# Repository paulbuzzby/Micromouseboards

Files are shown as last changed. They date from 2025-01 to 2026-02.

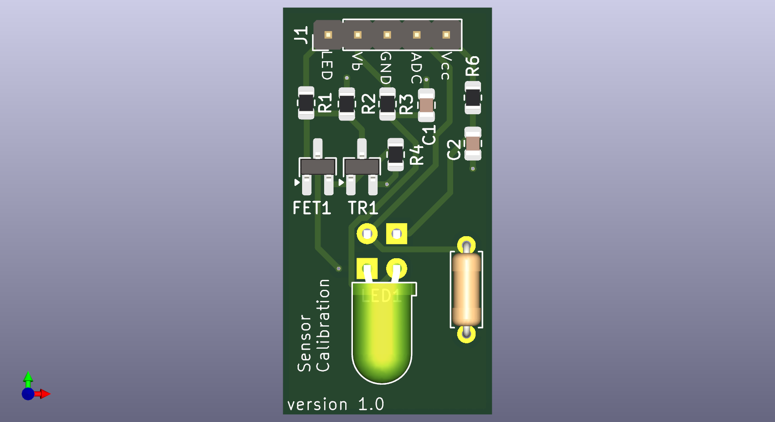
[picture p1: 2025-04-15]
SensorCalibrationBoard/SensorCalibrationBoardTop.png

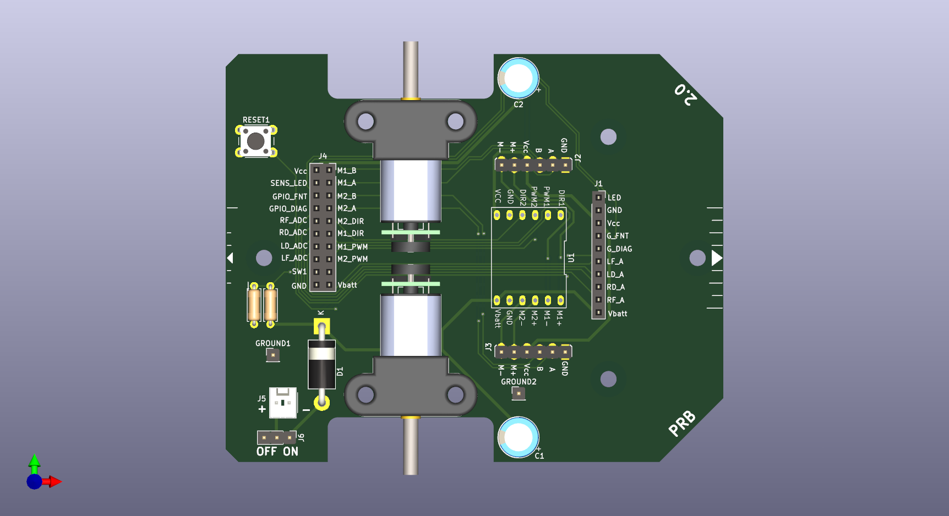
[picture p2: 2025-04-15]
SSChassisBoard/SSChassisBoardTop.png

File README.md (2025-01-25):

# Micromouseboards
Here are different sets of PCBs for various Micro Mouse applications. This is the start of me using KiCad. I make no promises that any of this works.

Some of these boards (MouseSMDUKMARSAdvancedBoard and MouseMainboardTemplate) started as UKMARS boards that can be found [Here](https://github.com/ukmars/ukmarsbot)

All credit to Peter Harrison for the original design of these boards

Circuit design for the other boards is credited to Duncan Louttit

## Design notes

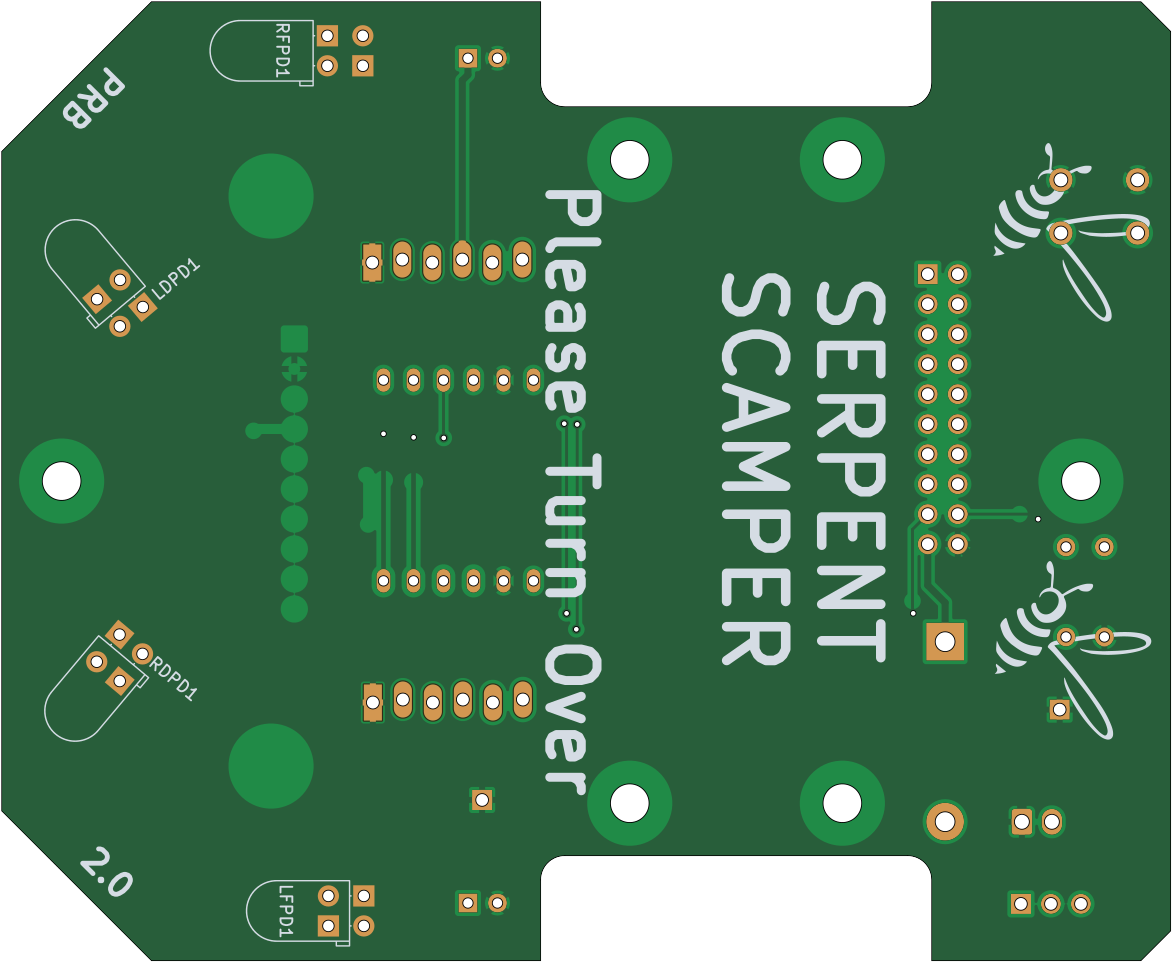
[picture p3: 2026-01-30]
docs/SSChassisAndSensorBoard/SSChassisAndSensorBoard_board_bottom.png

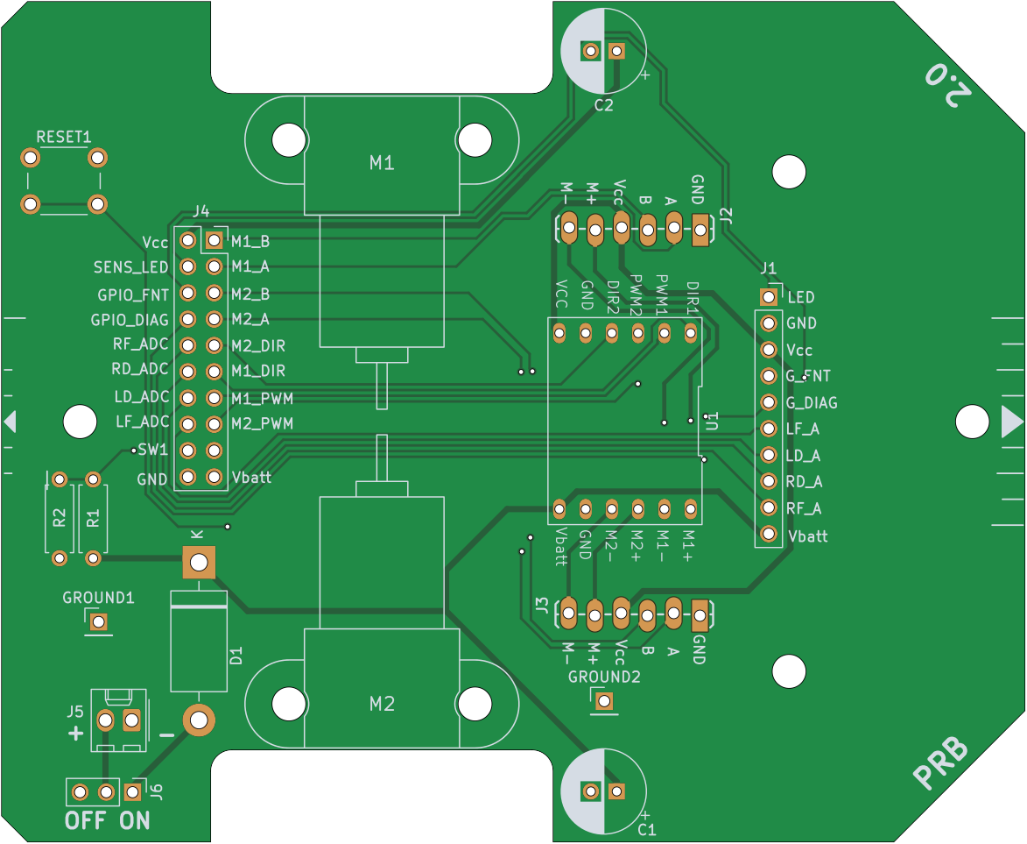
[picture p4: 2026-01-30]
docs/SSChassisBoard/SSChassisBoard_board_top.png

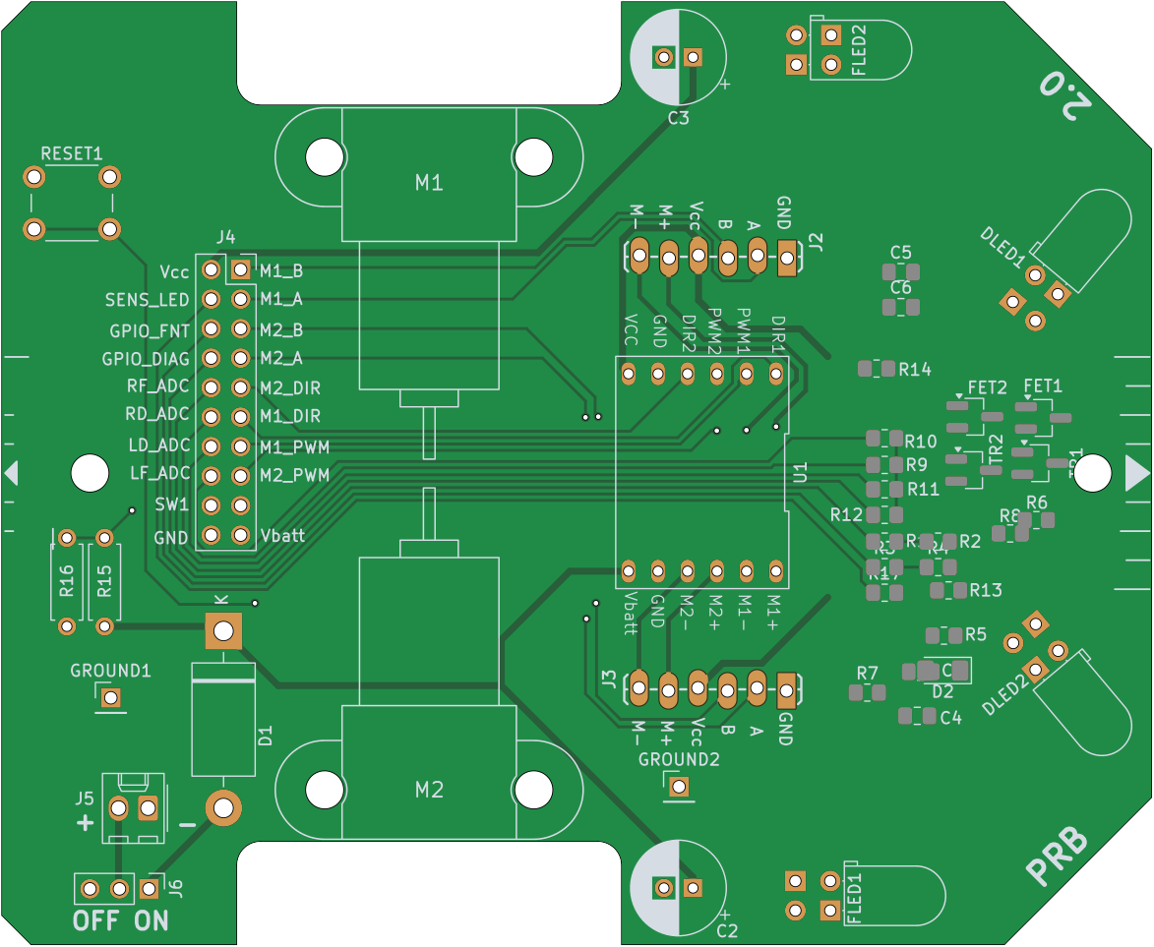
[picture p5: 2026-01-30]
docs/SSChassisAndSensorBoard/SSChassisAndSensorBoard_board_top.png

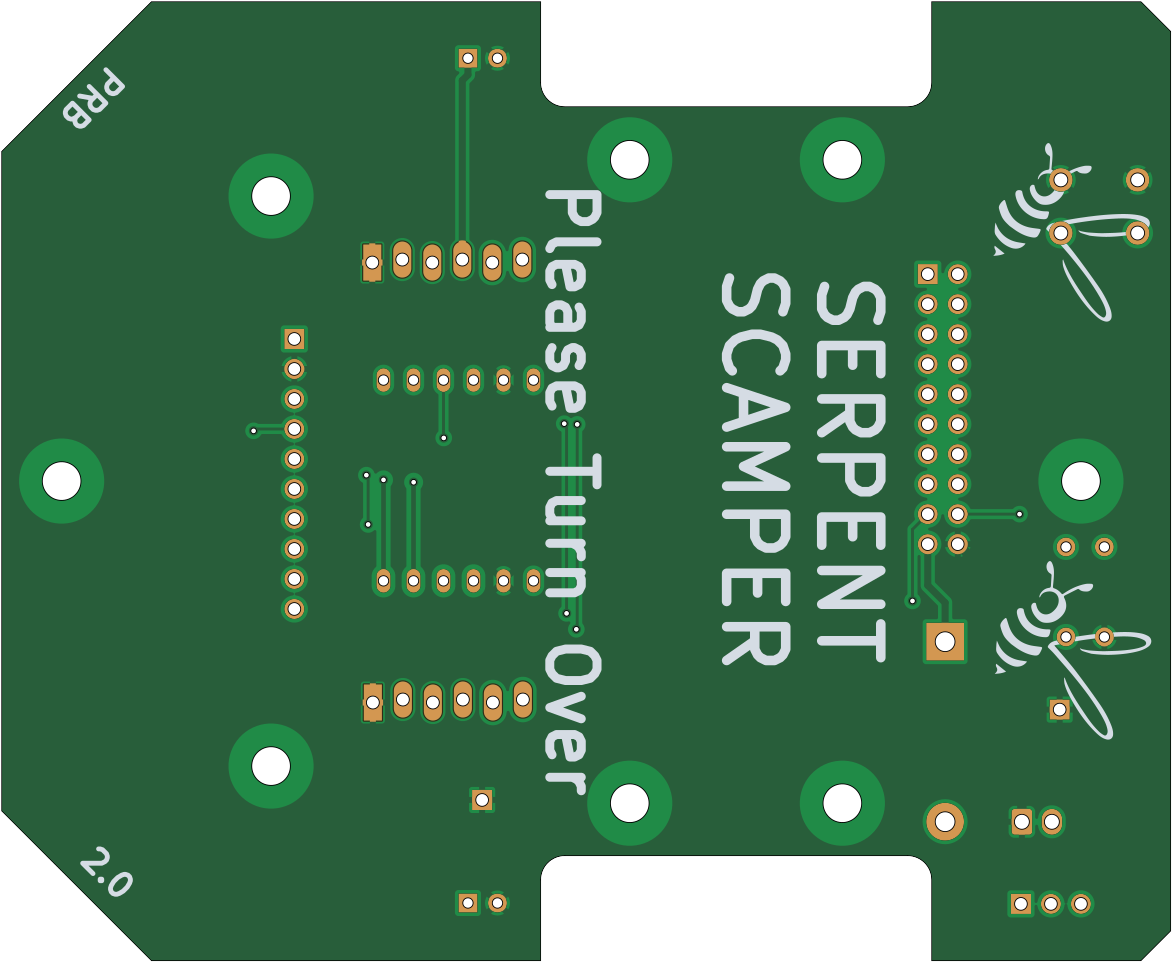
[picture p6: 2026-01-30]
docs/SSChassisBoard/SSChassisBoard_board_bottom.png

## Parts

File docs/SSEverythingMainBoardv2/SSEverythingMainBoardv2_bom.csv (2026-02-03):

Reference | Value | Qty | Note | Description
A1 | Arduino_Nano_RP2040_Connect | 1 |  | Arduino Nano board based on the RP2040 microcontroller with a dual-core 133 MHz ARM Cortex-M0+ processor, 264 kB SRAM, and up to 16 MB flash memory. Operates at 3.3V, with 5V Micro USB input and 4-20V VIN. Features Wi-Fi®, Bluetooth® LE, digital and analog pins, and supports SPI, I2C, UART, and PIO. Includes a 6-axis IMU, RGB LED, microphone, and cryptographic chip for secure communication.
C1 C2 C3 C5 C7 C8 C9 C10 | 10uF | 8 |  | Unpolarized capacitor
C4 C6 | 330uF, 16V | 2 | Maximum height is 10mm
D3 D4 D5 | LED | 3 |  | Light emitting diode
FLLED1 FRLED2 LDLED1 RDLED2 | TLCR5800 | 4 |  | Light emitting diode
GROUND1 GROUND2 J4 J5 J6 J8 | GROUND | 6 |  | Generic connector, single row, 01x01, script generated (kicad-library-utils/schlib/autogen/connector/) Generic connector, single row, 01x02, script generated (kicad-library-utils/schlib/autogen/connector/) Generic connector, single row, 01x05, script generated (kicad-library-utils/schlib/autogen/connector/) Generic connector, single row, 01x03, script generated (kicad-library-utils/schlib/autogen/connector/)
J1 J2 | CONN_06SILK_FEMALE_PTH | 2 | 6 pin header, 0.1", male
LDPD1 LFPD1 RDPD1 RFPD1 | BPW96B | 4 |  | Photodiode
M1 | Left MOTOR | 1 | commercial mounts need bushing for screws
M2 | Right MOTOR | 1 | commercial mounts need bushing for screws
Q1 Q2 Q3 Q4 | PBSS4160DS | 4
R3 R4 | 100K | 2 |  | Resistor
R5 R7 R15 R22 | 100R | 4 |  | Resistor
R1 R2 R17 R18 R19 R20 | 1K | 6 |  | Resistor
R21 | 1K0 | 1 |  | Resistor
R12 R14 R24 R25 | 220R | 4 |  | Resistor
R9 R10 R11 R13 | 2K2 | 4 |  | Resistor
R6 R8 R16 R23 | 4R7 | 4 |  | Resistor
SW1 | TACT_SW | 1 |  | TACT switch 6mm 4.5mm
U1 | DFRobot_DC_Controller | 1

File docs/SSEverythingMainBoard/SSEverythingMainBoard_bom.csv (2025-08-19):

Reference | Value | Qty | Note | Description
A1 | Arduino_Nano_RP2040_Connect | 1 |  | Arduino Nano board based on the RP2040 microcontroller with a dual-core 133 MHz ARM Cortex-M0+ processor, 264 kB SRAM, and up to 16 MB flash memory. Operates at 3.3V, with 5V Micro USB input and 4-20V VIN. Features Wi-Fi®, Bluetooth® LE, digital and analog pins, and supports SPI, I2C, UART, and PIO. Includes a 6-axis IMU, RGB LED, microphone, and cryptographic chip for secure communication.
C7 C8 C10 C12 | 0.1uF | 4
C1 C2 C3 C5 C9 C11 | 10uF | 6 |  | Unpolarized capacitor
C4 C6 | 330uF, 16V | 2 | Maximum height is 10mm
D3 D4 D5 | LED | 3 |  | Light emitting diode
D2 | SS34 | 1 | RS - 808-0433 | onsemi 40V 3A, Schottky Diode
DLED1 DLED2 FLED1 FLED2 | TLCR5800 | 4 |  | Light emitting diode
FET1 FET2 | PMV45EN2 | 2 |  | N-Channel MOSFET, 5.1 A, 30 V, 3-Pin SOT-23
GROUND1 GROUND2 J3 J4 J5 J6 | GROUND | 6 | 0.1" pitch, polarised, any type | Generic connector, single row, 01x01, script generated (kicad-library-utils/schlib/autogen/connector/) Generic connector, single row, 01x02, script generated (kicad-library-utils/schlib/autogen/connector/) Generic connector, single row, 01x05, script generated (kicad-library-utils/schlib/autogen/connector/)
J1 J2 | CONN_06SILK_FEMALE_PTH | 2 | 6 pin header, 0.1", male
LDPD1 LFPD1 RDPD1 RFPD1 | BPW96B | 4 |  | Photodiode
M1 | Left MOTOR | 1 | commercial mounts need bushing for screws
M2 | Right MOTOR | 1 | commercial mounts need bushing for screws
R3 R4 | 100K | 2 |  | Resistor
R5 R7 | 10R | 2 |  | Resistor
R19 | 180K | 1 |  | Resistor
R17 R18 | 1K | 2 |  | Resistor
R21 | 1K0 | 1 |  | Resistor
R1 R2 R12 R14 | 220R | 4 |  | Resistor
R20 | 68K | 1 |  | Resistor
R9 R10 R11 R13 | R | 4 |  | Resistor
R6 R8 | R56 | 2 |  | Resistor
SW1 | TACT_SW | 1 |  | TACT switch 6mm 4.5mm
TR1 TR2 | BC849 | 2 |  | 0.1A Ic, 30V Vce, NPN Transistor, SOT-23
U1 | DFRobot_DC_Controller | 1

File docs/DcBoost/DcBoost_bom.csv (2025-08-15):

Reference | Value | Qty | Note | Description
C2 | 10uF | 1 |  | Unpolarized capacitor
C1 | 2.2uF | 1 |  | Unpolarized capacitor
D1 | SS34 | 1 |  | Schottky diode, small symbol, filled shape
L1 | L4.7uH | 1 |  | Inductor
R2 | R10k | 1 |  | Resistor
R1 | R64.9k | 1 |  | Resistor
U1 | MIC2288 | 1 |  | DC Boost

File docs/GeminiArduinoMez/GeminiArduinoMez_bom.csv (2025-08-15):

Reference | Value | Qty | Note | Description
A1 | Arduino_Nano_RP2040_Connect | 1 |  | Arduino Nano board based on the RP2040 microcontroller with a dual-core 133 MHz ARM Cortex-M0+ processor, 264 kB SRAM, and up to 16 MB flash memory. Operates at 3.3V, with 5V Micro USB input and 4-20V VIN. Features Wi-Fi®, Bluetooth® LE, digital and analog pins, and supports SPI, I2C, UART, and PIO. Includes a 6-axis IMU, RGB LED, microphone, and cryptographic chip for secure communication.
D1 | LED | 1 |  | Light emitting diode
J1 J3 J4 | Conn_01x16 | 3 |  | Generic connector, single row, 01x16, script generated (kicad-library-utils/schlib/autogen/connector/) Generic connector, single row, 01x06, script generated (kicad-library-utils/schlib/autogen/connector/)
R2 | 180K | 1 |  | Resistor
R1 | 680R | 1 |  | Resistor
R3 | 68K | 1 |  | Resistor
SW1 | TACT_SW | 1 |  | TACT switch 6mm 4.5mm

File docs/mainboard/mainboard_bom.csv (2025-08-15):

Reference | Value | Qty | Note | Description
C2 | 330uF, 16V | 1 | Maximum height is 10mm
D1 | 1N5401 | 1 | > 2A rectifier. Shottky is good
J2 J3 | CONN_06SILK_FEMALE_PTH | 2 | 6 pin header, 0.1", male
J4 | POWER | 1 | 0.1" pitch, polarised, any type
J1 | SENSORS | 1 | 14 pin header, 0.1", male
M1 | Left Motor | 1 | commercial mounts need bushing for screws
M2 | Right Motor | 1 | commercial mounts need bushing for screws
S1 | sub-miniature, SPDT | 1 | Toggle or slide, 0.1" pitch pins, EG Salecom TS-4-TE1CR-E-H-Z03

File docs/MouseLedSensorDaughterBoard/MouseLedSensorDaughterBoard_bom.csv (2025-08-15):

Reference | Value | Qty | Note | Description
J2 | Conn_01x04 | 1 |  | Generic connector, single row, 01x04, script generated (kicad-library-utils/schlib/autogen/connector/)
LED1 | TLCR5800 | 1 |  | Light emitting diode
PD3 | BPW96B | 1 |  | Phototransistor NPN
PD2 | QSB34 | 1 |  | Photodiode VEMD4010X01

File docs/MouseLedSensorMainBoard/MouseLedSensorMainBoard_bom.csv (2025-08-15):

Reference | Value | Qty | Note | Description
C1 C2 | 10uF | 2 |  | Unpolarized capacitor
FET1 | BSH108,215 | 1 |  | 5mA Idss, 30V Vgs, N-Channel JFET, SOT-23
J1 J2 | Conn_01x05 | 2 |  | Generic connector, single row, 01x06, script generated (kicad-library-utils/schlib/autogen/connector/) Generic connector, single row, 01x08, script generated (kicad-library-utils/schlib/autogen/connector/)
R3 | 10R | 1 |  | Resistor
R1 R4 | 220R | 2 |  | Resistor
RPD1 | 100K | 1 |  | Resistor
RSENSE1 | R56 | 1 |  | Resistor
S1R1 S2R1 | R | 2 |  | Resistor
TR1 | BC849 | 1 |  | 0.1A Ic, 30V Vce, NPN Transistor, SOT-23

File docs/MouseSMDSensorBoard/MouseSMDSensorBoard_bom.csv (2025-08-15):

Reference | Value | Qty | Note | Description
C1 C2 | 10uF | 2 |  | Unpolarized capacitor
FET1 | PMV45EN2 | 1 |  | N-Channel MOSFET, 5.1 A, 30 V, 3-Pin SOT-23
J1 | Conn_01x05 | 1 |  | Generic connector, single row, 01x05, script generated (kicad-library-utils/schlib/autogen/connector/)
LED1 | TLCR5800 | 1 |  | Light emitting diode
PD2 | BPW96B | 1 |  | Photodiode
PD1 | QSB34 | 1 |  | Photodiode QSB34 (RS part number 805-0508)
R2 | 100K | 1 |  | Resistor
R3 | 10R | 1 |  | Resistor
R1 R6 | 220R | 2 |  | Resistor
R5 | R | 1 |  | Resistor
R4 | R56 | 1 |  | Resistor
TR1 | BC849 | 1 |  | 0.1A Ic, 30V Vce, NPN Transistor, SOT-23

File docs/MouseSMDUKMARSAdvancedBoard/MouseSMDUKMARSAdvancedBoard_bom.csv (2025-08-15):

Reference | Value | Qty | Note | Description
C1 C2 C3 C4 | 10uF | 4 |  | Unpolarized capacitor
D1 | LED | 1 |  | Light emitting diode
DLED1 DLED2 FLED1 FLED2 | TLCR5800 | 4 |  | Light emitting diode
FET1 FET2 | PMV45EN2 | 2 |  | N-Channel MOSFET, 5.1 A, 30 V, 3-Pin SOT-23
J1 | Conn_01x10 | 1 |  | Generic connector, single row, 01x10, script generated (kicad-library-utils/schlib/autogen/connector/)
LDPD1 LFPD1 RDPD1 RFPD2 | BPW96B | 4 |  | Photodiode
R3 R4 | 100K | 2 |  | Resistor
R5 R7 | 10R | 2 |  | Resistor
R15 | 1K0 | 1 |  | Resistor
R1 R2 R12 R14 | 220R | 4 |  | Resistor
R9 R10 R11 R13 | R | 4 |  | Resistor
R6 R8 | R56 | 2 |  | Resistor
TR1 TR2 | BC849 | 2 |  | 0.1A Ic, 30V Vce, NPN Transistor, SOT-23

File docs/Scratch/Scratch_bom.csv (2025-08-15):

Reference | Value | Qty | Note | Description
C1 C2 | 330uF, 16V | 2 | Maximum height is 10mm
D1 | 1N5401 | 1 | > 2A rectifier. Shottky is good
GROUND1 GROUND2 J1 J4 J5 J6 | GROUND | 6 | 0.1" pitch, polarised, any type | Generic connector, single row, 01x01, script generated (kicad-library-utils/schlib/autogen/connector/) Generic connector, single row, 01x10, script generated (kicad-library-utils/schlib/autogen/connector/) Generic connector, double row, 02x10, odd/even pin numbering scheme (row 1 odd numbers, row 2 even numbers), script generated (kicad-library-utils/schlib/autogen/connector/) Generic connector, single row, 01x03, script generated (kicad-library-utils/schlib/autogen/connector/)
J2 J3 | CONN_06SILK_FEMALE_PTH | 2 | 6 pin header, 0.1", male
M1 | Left MOTOR | 1 | commercial mounts need bushing for screws
M2 | Right MOTOR | 1 | commercial mounts need bushing for screws
R1 | 180K | 1 |  | Resistor
R2 | 68K | 1 |  | Resistor
RESET1 | TACT_SW | 1 |  | TACT switch 6mm 4.5mm
U1 | DFRobot_DC_Controller | 1
U2 | LMV331 | 1 |  | Single General-Purpose Low-Voltage Comparator, SOT-23-5/SC-70-5

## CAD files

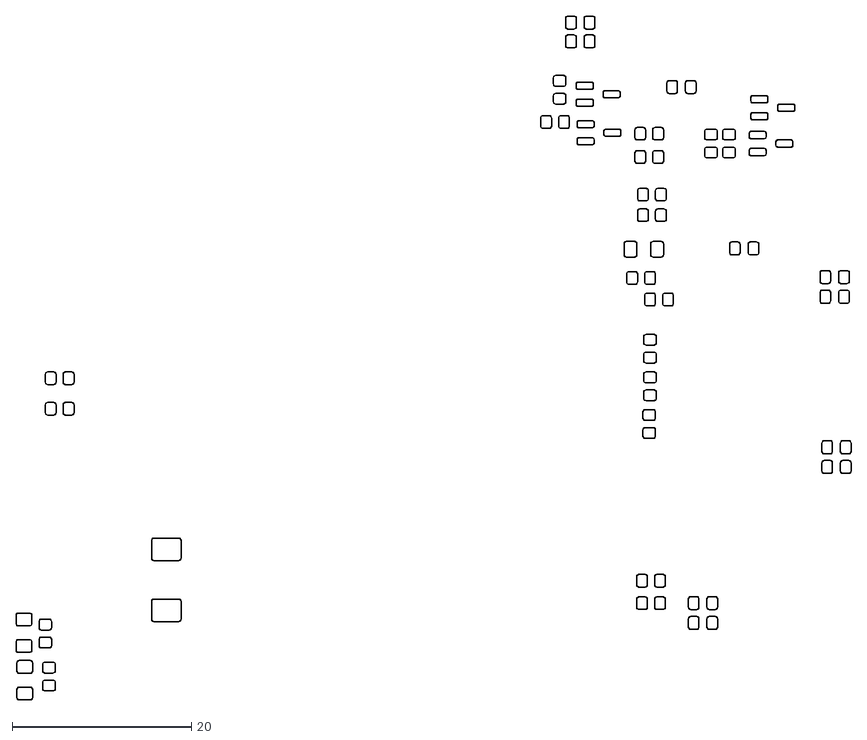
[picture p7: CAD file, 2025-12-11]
SSEverythingMainBoard/SSEverythingMainBoard-PasteTop.dxf
93.2 x 76.3

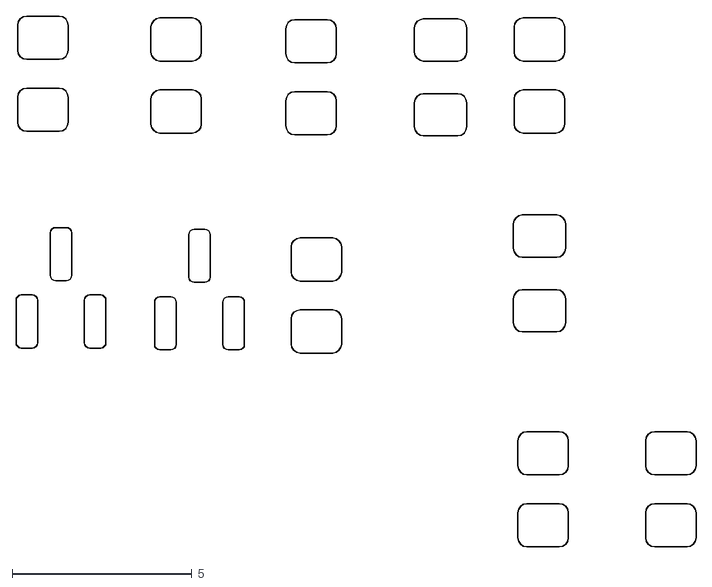
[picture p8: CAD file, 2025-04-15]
Stencils/MouseLedSensorMainBoard-PasteTop.dxf
18.9 x 14.8

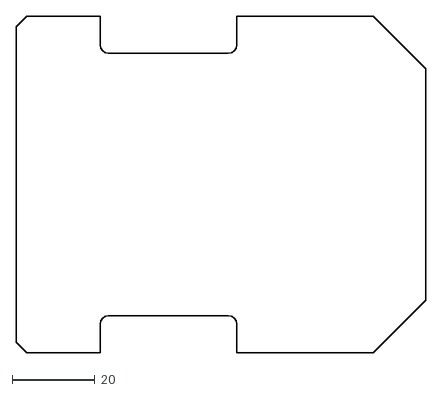
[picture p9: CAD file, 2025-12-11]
SSEverythingMainBoard/SSEverythingMainBoard-EdgeCuts.dxf
99.1 x 81.3

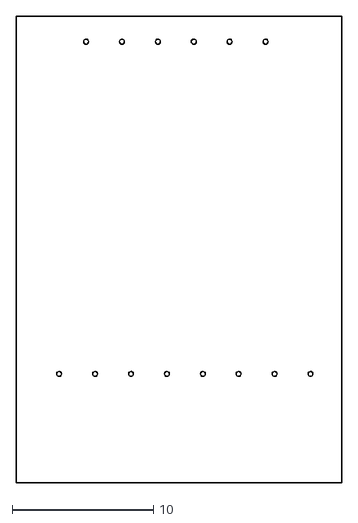
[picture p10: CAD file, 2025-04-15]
Stencils/MouseLedSensorMainBoard-EdgeCuts.dxf
23.0 x 33.0

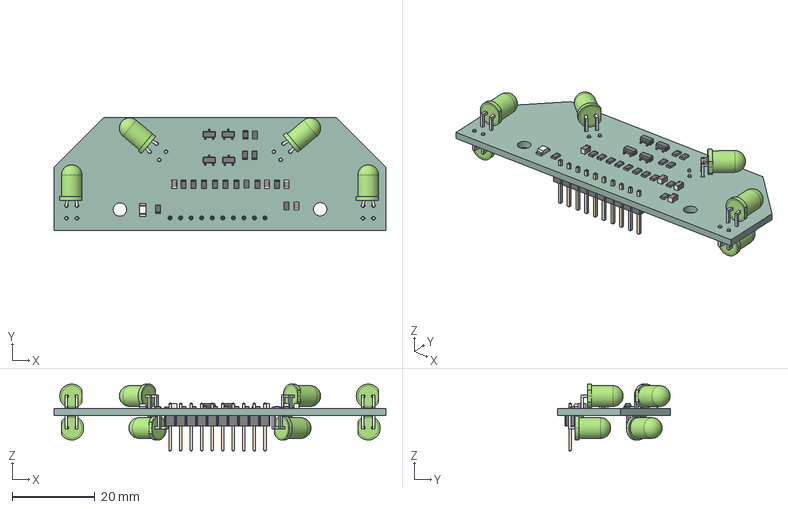
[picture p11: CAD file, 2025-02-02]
MouseSMDUKMARSAdvancedBoard/MouseSMDUKMARSAdvancedBoard.step
80.0 x 27.3 x 16.1 mm
R_0805_2012Metric x 15
LED_D5.0mm_Horizontal_O1.27mm_Z3.0mm x 8
SOT_23 x 4
C_0805_2012Metric x 4
LED_1206_3216Metric
PinHeader_1x10_P254mm_Vertical
MouseSMDUKMARSAdvancedBoard_PCB

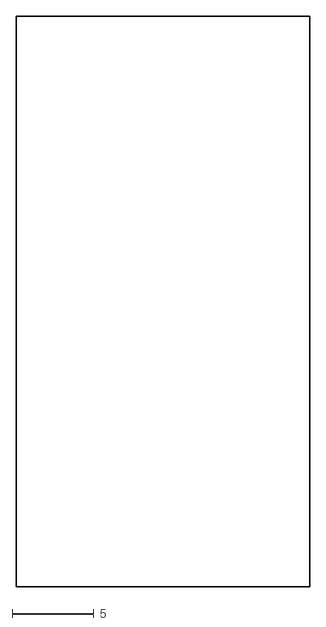
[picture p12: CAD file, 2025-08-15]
SensorCalibrationBoard/SensorCalibrationBoard-EdgeCuts.dxf
18.0 x 35.0

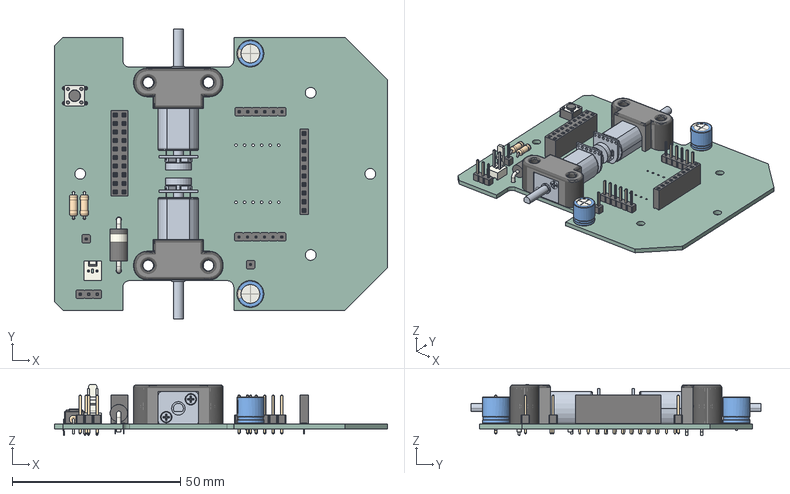
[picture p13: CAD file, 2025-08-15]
SSChassisBoard/SSChassisBoard.step
99.1 x 86.4 x 15.3 mm
SW_PUSH_6mm
PinHeader_1x03_P254mm_Vertical
R_Axial_DIN0207_L63mm_D25mm_P762mm_Horizontal x 2
motor_encoder_covered x 2
CP_Radial_D80mm_P250mm x 2
PinHeader_1x01_P254mm_Vertical x 2
PinHeader_1x06_P254mm_Vertical x 2
D_DO-201AD_P15.24mm_Horizontal
PinSocket_1x10_P2.54mm_Vertical
Molex_AE_6410_02A
PinSocket_2x10_P2.54mm_Vertical
SSChassisBoard_PCB

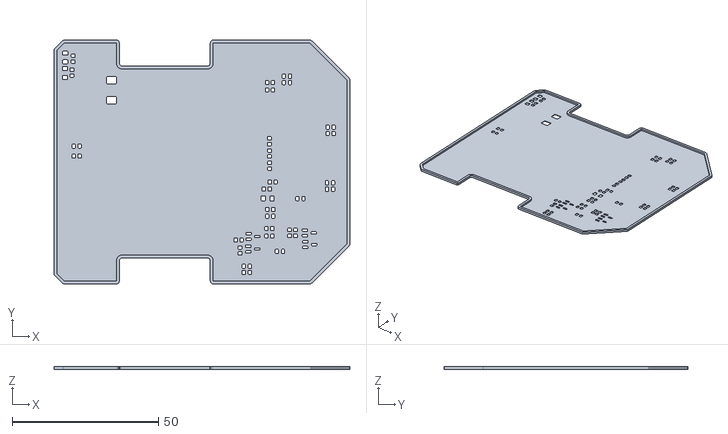
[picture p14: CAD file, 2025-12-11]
SSEverythingMainBoard/topStencil.stl
101.1 x 83.3 x 0.9

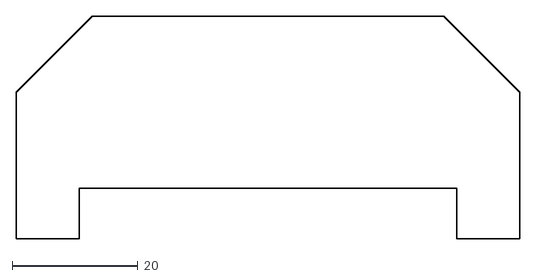
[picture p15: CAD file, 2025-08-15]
SSWallSensorBoard/SSWallSensorBoard-EdgeCuts.dxf
80.0 x 35.3

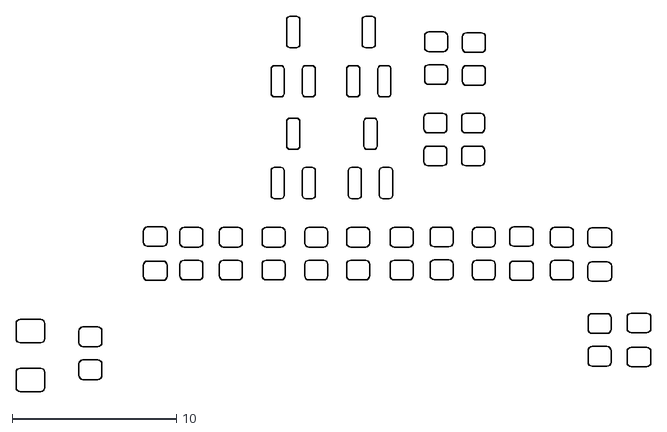
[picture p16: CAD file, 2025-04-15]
Stencils/MouseSMDUKMARSAdvancedBoard-PasteTop.dxf
38.6 x 22.8

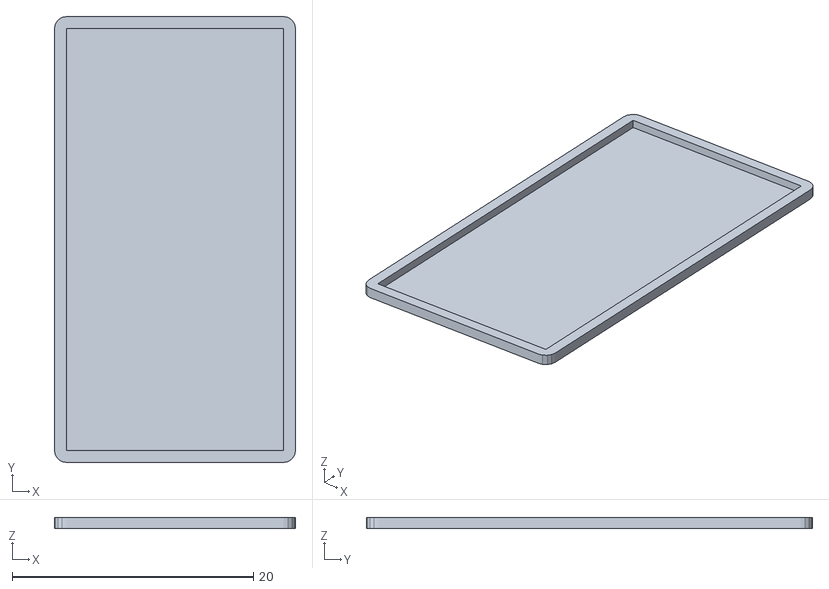
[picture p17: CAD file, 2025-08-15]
SensorCalibrationBoard/bottomStencil.stl
20.0 x 37.0 x 0.9

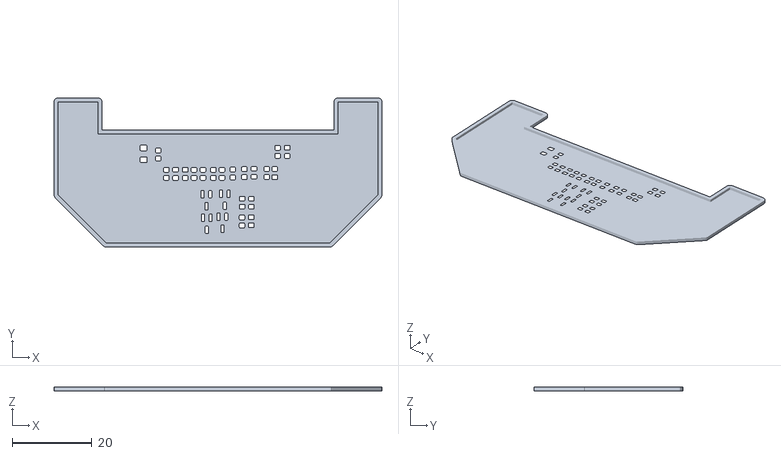
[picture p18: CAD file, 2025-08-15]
SSWallSensorBoard/topStencil.stl
82.0 x 37.3 x 0.9

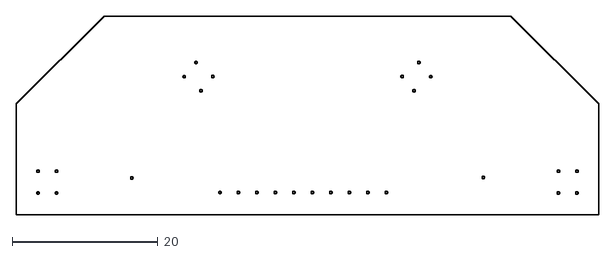
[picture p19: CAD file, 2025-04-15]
Stencils/MouseSMDUKMARSAdvancedBoard-EdgeCuts.dxf
80.0 x 27.3

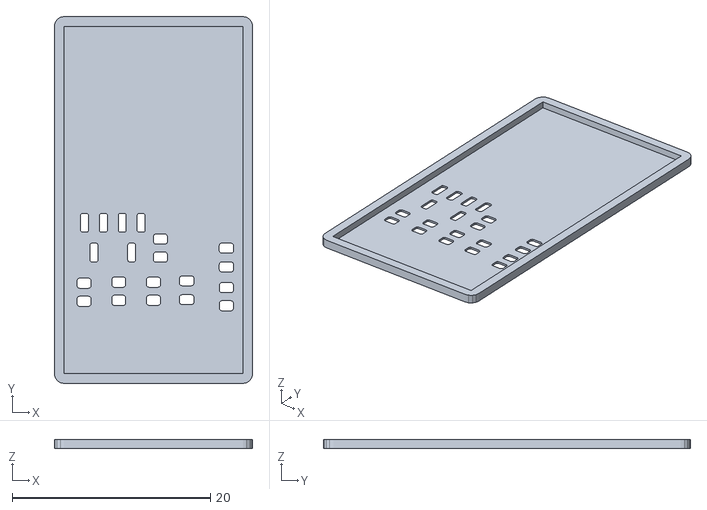
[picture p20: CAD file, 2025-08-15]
SensorCalibrationBoard/topStencil.stl
20.0 x 37.0 x 0.9

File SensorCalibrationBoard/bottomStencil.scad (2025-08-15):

// Generated by SolidPython 1.1.3 on 2025-04-25 20:07:26
$fa = 0.4; $fs = 0.4;


rotate(a = 0, v = [1, 0, 0]) {
	difference() {
		scale(v = [1, 1, 1]) {
			difference() {
				linear_extrude(height = 0.9000000000) {
					offset(r = 1.0000000000) {
						import(file = "E:/sourcecode/Micromouseboards/SensorCalibrationBoard/SensorCalibrationBoard-EdgeCuts.dxf", origin = [0, 0]);
					}
				}
				translate(v = [0, 0, 0.2000000000]) {
					linear_extrude(height = 0.9000000000) {
						translate(v = [0, 0, 0]) {
							import(file = "E:/sourcecode/Micromouseboards/SensorCalibrationBoard/SensorCalibrationBoard-EdgeCuts.dxf", origin = [0, 0]);
						}
					}
				}
			}
		}
		linear_extrude(center = true, height = 0.8000000000) {
			translate(v = [0, 0, 0]) {
				import(file = "E:/sourcecode/Micromouseboards/SensorCalibrationBoard/SensorCalibrationBoard-PasteBottom.dxf", origin = [0, 0]);
			}
		}
	}
}
/***********************************************
*********      SolidPython code:      **********
************************************************
 
from pcbnewTransition import pcbnew
import numpy as np
import json
from collections import OrderedDict
from kikit.common import *
from kikit.defs import *
from kikit.substrate import Substrate, extractRings, toShapely, linestringToKicad
from kikit.export import gerberImpl, pasteDxfExport
from kikit.export import exportSettingsJlcpcb
import solid
import solid.utils
import subprocess
import shutil
from kikit.common import removeComponents, parseReferences

from shapely.geometry import Point


OUTER_BORDER = fromMm(7.5)
INNER_BORDER = fromMm(5)
MOUNTING_HOLES_COUNT = 3
MOUNTING_HOLE_R = fromMm(1)
HOLE_SPACING = fromMm(20)

def addBottomCounterpart(board, item):
    item = item.Duplicate()
    item.SetLayer(Layer.B_Paste)
    board.Add(item)

def addRoundedCorner(board, center, start, end, thickness):
    corner = pcbnew.PCB_SHAPE()
    corner.SetShape(STROKE_T.S_ARC)
    corner.SetCenter(toKiCADPoint((center[0], center[1])))
    corner.SetStart(toKiCADPoint((start[0], start[1])))

    if np.cross(start - center, end - center) > 0:
        corner.SetArcAngleAndEnd(fromDegrees(90), True)
    else:
        corner.SetArcAngleAndEnd(fromDegrees(-90), True)
    corner.SetWidth(thickness)
    corner.SetLayer(Layer.F_Paste)
    board.Add(corner)
    addBottomCounterpart(board, corner)

def addLine(board, start, end, thickness):
    line = pcbnew.PCB_SHAPE()
    line.SetShape(STROKE_T.S_SEGMENT)
    line.SetStart(toKiCADPoint((start[0], start[1])))
    line.SetEnd(toKiCADPoint((end[0], end[1])))
    line.SetWidth(thickness)
    line.SetLayer(Layer.F_Paste)
    board.Add(line)
    addBottomCounterpart(board, line)

def addBite(board, origin, direction, normal, thickness):
    """
    Adds a bite to the stencil, direction points to the bridge, normal points
    inside the stencil
    """
    direction = normalize(direction) * thickness
    normal = normalize(normal) * thickness
    center = toKiCADPoint((origin[0], origin[1])) + toKiCADPoint((normal[0], normal[1]))
    start = origin
    end = center + toKiCADPoint((direction[0], direction[1]))
    # addLine(board, end, end + normal / 2, thickness)
    addRoundedCorner(board, center, start, end, thickness)

def numberOfCuts(length, bridgeWidth, bridgeSpacing):
    """
    Return number of bridges which fit inside the length and cut length
    """
    count = int(np.floor((length + bridgeWidth) / (bridgeWidth + bridgeSpacing)))
    cutLength = (length - (count - 1) * bridgeWidth) / count
    return count, cutLength

def addFrame(board, rect, bridgeWidth, bridgeSpacing, clearance):
    """
    Add rectangular frame to the board
    """
    R=fromMm(1)

    corners = [
        (tl(rect), toKiCADPoint((R, 0)), toKiCADPoint((0, R))), # TL
        (tr(rect), toKiCADPoint((0, R)), toKiCADPoint((-R, 0))), # TR
        (br(rect), toKiCADPoint((-R, 0)), toKiCADPoint((0, -R))), # BR
        (bl(rect), toKiCADPoint((0, -R)), toKiCADPoint((R, 0))) # BL
    ]
    for c, sOffset, eOffset in corners:
        addRoundedCorner(board, c + sOffset + eOffset, c + sOffset, c + eOffset, clearance)

    count, cutLength = numberOfCuts(rect.GetWidth() - 2 * R, bridgeWidth, bridgeSpacing)
    for i in range(count):
        start = rect.GetX() + R + i * bridgeWidth + i * cutLength
        end = start + cutLength

        y1, y2 = rect.GetY(), rect.GetY() + rect.GetHeight()
        addLine(board, toKiCADPoint((start, y1)), toKiCADPoint((end, y1)), clearance)
        if i != 0:
            addBite(board, toKiCADPoint((start, y1)), toKiCADPoint((-1, 0)), toKiCADPoint((0, 1)), clearance)
        if i != count - 1:
            addBite(board, toKiCADPoint((end, y1)), toKiCADPoint((1, 0)), toKiCADPoint((0, 1)), clearance)
        addLine(board, toKiCADPoint((start, y2)), toKiCADPoint((end, y2)), clearance)
        if i != 0:
            addBite(board, toKiCADPoint((start, y2)), toKiCADPoint((-1, 0)), toKiCADPoint((0, -1)), clearance)
        if i != count - 1:
            addBite(board, toKiCADPoint((end, y2)), toKiCADPoint((1, 0)), toKiCADPoint((0, -1)), clearance)

    count, cutLength = numberOfCuts(rect.GetHeight() - 2 * R, bridgeWidth, bridgeSpacing)
    for i in range(count):
        start = rect.GetY() + R + i * bridgeWidth + i * cutLength
        end = start + cutLength

        x1, x2 = rect.GetX(), rect.GetX() + rect.GetWidth()
        addLine(board, toKiCADPoint((x1, start)), toKiCADPoint((x1, end)), clearance)
        if i != 0:
            addBite(board, toKiCADPoint((x1, start)), toKiCADPoint((0, -1)), toKiCADPoint((1, 0)), clearance)
        if i != count - 1:
            addBite(board, toKiCADPoint((x1, end)), toKiCADPoint((0, 1)), toKiCADPoint((1, 0)), clearance)
        addLine(board, toKiCADPoint((x2, start)), toKiCADPoint((x2, end)), clearance)
        if i != 0:
            addBite(board, toKiCADPoint((x2, start)), toKiCADPoint((0, -1)), toKiCADPoint((-1, 0)), clearance)
        if i != count - 1:
            addBite(board, toKiCADPoint((x2, end)), toKiCADPoint((0, 1)), toKiCADPoint((-1, 0)), clearance)

def addHole(board, position, radius):
    circle = pcbnew.PCB_SHAPE()
    circle.SetShape(STROKE_T.S_CIRCLE)
    circle.SetCenter(toKiCADPoint((position[0], position[1])))
    # Set 3'oclock point of the circle to set radius
    circle.SetEnd(toKiCADPoint((position[0], position[1])) + toKiCADPoint((radius/2, 0)))

    circle.SetWidth(radius)
    circle.SetLayer(Layer.F_Paste)
    board.Add(circle)
    addBottomCounterpart(board, circle)

def addJigFrame(board, jigFrameSize, bridgeWidth=fromMm(2),
                bridgeSpacing=fromMm(10), clearance=fromMm(0.5)):
    """
    Given a Pcbnew board finds the board outline and creates a stencil for
    KiKit's stencil jig.

    Mainly, adds mounting holes and mouse bites to define the panel outline.

    jigFrameSize is a tuple (width, height).
    """
    bBox = findBoardBoundingBox(board)
    frameSize = rectByCenter(rectCenter(bBox),
        jigFrameSize[0] + 2 * (OUTER_BORDER + INNER_BORDER),
        jigFrameSize[1] + 2 * (OUTER_BORDER + INNER_BORDER))
    cutSize = rectByCenter(rectCenter(bBox),
        jigFrameSize[0] + 2 * (OUTER_BORDER + INNER_BORDER) - fromMm(1),
        jigFrameSize[1] + 2 * (OUTER_BORDER + INNER_BORDER) - fromMm(1))
    addFrame(board, cutSize, bridgeWidth, bridgeSpacing, clearance)

    for i in range(MOUNTING_HOLES_COUNT):
        x = frameSize.GetX() + OUTER_BORDER / 2 + (i + 1) * (frameSize.GetWidth() - OUTER_BORDER) / (MOUNTING_HOLES_COUNT + 1)
        addHole(board, toKiCADPoint((x, OUTER_BORDER / 2 + frameSize.GetY())), MOUNTING_HOLE_R)
        addHole(board, toKiCADPoint((x, - OUTER_BORDER / 2 +frameSize.GetY() + frameSize.GetHeight())), MOUNTING_HOLE_R)
    for i in range(MOUNTING_HOLES_COUNT):
        y = frameSize.GetY() + OUTER_BORDER / 2 + (i + 1) * (frameSize.GetHeight() - OUTER_BORDER) / (MOUNTING_HOLES_COUNT + 1)
        addHole(board, toKiCADPoint((OUTER_BORDER / 2 + frameSize.GetX(), y)), MOUNTING_HOLE_R)
        addHole(board, toKiCADPoint((- OUTER_BORDER / 2 +frameSize.GetX() + frameSize.GetWidth(), y)), MOUNTING_HOLE_R)

    PIN_TOLERANCE = fromMm(0.05)
    addHole(board, tl(frameSize) + toKiCADPoint((OUTER_BORDER / 2, OUTER_BORDER / 2)), MOUNTING_HOLE_R + PIN_TOLERANCE)
    addHole(board, tr(frameSize) + toKiCADPoint((-OUTER_BORDER / 2, OUTER_BORDER / 2)), MOUNTING_HOLE_R + PIN_TOLERANCE)
    addHole(board, br(frameSize) + toKiCADPoint((-OUTER_BORDER / 2, -OUTER_BORDER / 2)), MOUNTING_HOLE_R + PIN_TOLERANCE)
    addHole(board, bl(frameSize) + toKiCADPoint((OUTER_BORDER / 2, -OUTER_BORDER / 2)), MOUNTING_HOLE_R + PIN_TOLERANCE)
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

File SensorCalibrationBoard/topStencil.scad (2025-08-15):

// Generated by SolidPython 1.1.3 on 2025-04-25 20:07:27
$fa = 0.4; $fs = 0.4;


rotate(a = 180, v = [1, 0, 0]) {
	difference() {
		scale(v = [1, 1, -1]) {
			difference() {
				linear_extrude(height = 0.9000000000) {
					offset(r = 1.0000000000) {
						import(file = "E:/sourcecode/Micromouseboards/SensorCalibrationBoard/SensorCalibrationBoard-EdgeCuts.dxf", origin = [0, 0]);
					}
				}
				translate(v = [0, 0, 0.2000000000]) {
					linear_extrude(height = 0.9000000000) {
						translate(v = [0, 0, 0]) {
							import(file = "E:/sourcecode/Micromouseboards/SensorCalibrationBoard/SensorCalibrationBoard-EdgeCuts.dxf", origin = [0, 0]);
						}
					}
				}
			}
		}
		linear_extrude(center = true, height = 0.8000000000) {
			translate(v = [0, 0, 0]) {
				import(file = "E:/sourcecode/Micromouseboards/SensorCalibrationBoard/SensorCalibrationBoard-PasteTop.dxf", origin = [0, 0]);
			}
		}
	}
}
/***********************************************
*********      SolidPython code:      **********
************************************************
 
from pcbnewTransition import pcbnew
import numpy as np
import json
from collections import OrderedDict
from kikit.common import *
from kikit.defs import *
from kikit.substrate import Substrate, extractRings, toShapely, linestringToKicad
from kikit.export import gerberImpl, pasteDxfExport
from kikit.export import exportSettingsJlcpcb
import solid
import solid.utils
import subprocess
import shutil
from kikit.common import removeComponents, parseReferences

from shapely.geometry import Point


OUTER_BORDER = fromMm(7.5)
INNER_BORDER = fromMm(5)
MOUNTING_HOLES_COUNT = 3
MOUNTING_HOLE_R = fromMm(1)
HOLE_SPACING = fromMm(20)

def addBottomCounterpart(board, item):
    item = item.Duplicate()
    item.SetLayer(Layer.B_Paste)
    board.Add(item)

def addRoundedCorner(board, center, start, end, thickness):
    corner = pcbnew.PCB_SHAPE()
    corner.SetShape(STROKE_T.S_ARC)
    corner.SetCenter(toKiCADPoint((center[0], center[1])))
    corner.SetStart(toKiCADPoint((start[0], start[1])))

    if np.cross(start - center, end - center) > 0:
        corner.SetArcAngleAndEnd(fromDegrees(90), True)
    else:
        corner.SetArcAngleAndEnd(fromDegrees(-90), True)
    corner.SetWidth(thickness)
    corner.SetLayer(Layer.F_Paste)
    board.Add(corner)
    addBottomCounterpart(board, corner)

def addLine(board, start, end, thickness):
    line = pcbnew.PCB_SHAPE()
    line.SetShape(STROKE_T.S_SEGMENT)
    line.SetStart(toKiCADPoint((start[0], start[1])))
    line.SetEnd(toKiCADPoint((end[0], end[1])))
    line.SetWidth(thickness)
    line.SetLayer(Layer.F_Paste)
    board.Add(line)
    addBottomCounterpart(board, line)

def addBite(board, origin, direction, normal, thickness):
    """
    Adds a bite to the stencil, direction points to the bridge, normal points
    inside the stencil
    """
    direction = normalize(direction) * thickness
    normal = normalize(normal) * thickness
    center = toKiCADPoint((origin[0], origin[1])) + toKiCADPoint((normal[0], normal[1]))
    start = origin
    end = center + toKiCADPoint((direction[0], direction[1]))
    # addLine(board, end, end + normal / 2, thickness)
    addRoundedCorner(board, center, start, end, thickness)

def numberOfCuts(length, bridgeWidth, bridgeSpacing):
    """
    Return number of bridges which fit inside the length and cut length
    """
    count = int(np.floor((length + bridgeWidth) / (bridgeWidth + bridgeSpacing)))
    cutLength = (length - (count - 1) * bridgeWidth) / count
    return count, cutLength

def addFrame(board, rect, bridgeWidth, bridgeSpacing, clearance):
    """
    Add rectangular frame to the board
    """
    R=fromMm(1)

    corners = [
        (tl(rect), toKiCADPoint((R, 0)), toKiCADPoint((0, R))), # TL
        (tr(rect), toKiCADPoint((0, R)), toKiCADPoint((-R, 0))), # TR
        (br(rect), toKiCADPoint((-R, 0)), toKiCADPoint((0, -R))), # BR
        (bl(rect), toKiCADPoint((0, -R)), toKiCADPoint((R, 0))) # BL
    ]
    for c, sOffset, eOffset in corners:
        addRoundedCorner(board, c + sOffset + eOffset, c + sOffset, c + eOffset, clearance)

    count, cutLength = numberOfCuts(rect.GetWidth() - 2 * R, bridgeWidth, bridgeSpacing)
    for i in range(count):
        start = rect.GetX() + R + i * bridgeWidth + i * cutLength
        end = start + cutLength

        y1, y2 = rect.GetY(), rect.GetY() + rect.GetHeight()
        addLine(board, toKiCADPoint((start, y1)), toKiCADPoint((end, y1)), clearance)
        if i != 0:
            addBite(board, toKiCADPoint((start, y1)), toKiCADPoint((-1, 0)), toKiCADPoint((0, 1)), clearance)
        if i != count - 1:
            addBite(board, toKiCADPoint((end, y1)), toKiCADPoint((1, 0)), toKiCADPoint((0, 1)), clearance)
        addLine(board, toKiCADPoint((start, y2)), toKiCADPoint((end, y2)), clearance)
        if i != 0:
            addBite(board, toKiCADPoint((start, y2)), toKiCADPoint((-1, 0)), toKiCADPoint((0, -1)), clearance)
        if i != count - 1:
            addBite(board, toKiCADPoint((end, y2)), toKiCADPoint((1, 0)), toKiCADPoint((0, -1)), clearance)

    count, cutLength = numberOfCuts(rect.GetHeight() - 2 * R, bridgeWidth, bridgeSpacing)
    for i in range(count):
        start = rect.GetY() + R + i * bridgeWidth + i * cutLength
        end = start + cutLength

        x1, x2 = rect.GetX(), rect.GetX() + rect.GetWidth()
        addLine(board, toKiCADPoint((x1, start)), toKiCADPoint((x1, end)), clearance)
        if i != 0:
            addBite(board, toKiCADPoint((x1, start)), toKiCADPoint((0, -1)), toKiCADPoint((1, 0)), clearance)
        if i != count - 1:
            addBite(board, toKiCADPoint((x1, end)), toKiCADPoint((0, 1)), toKiCADPoint((1, 0)), clearance)
        addLine(board, toKiCADPoint((x2, start)), toKiCADPoint((x2, end)), clearance)
        if i != 0:
            addBite(board, toKiCADPoint((x2, start)), toKiCADPoint((0, -1)), toKiCADPoint((-1, 0)), clearance)
        if i != count - 1:
            addBite(board, toKiCADPoint((x2, end)), toKiCADPoint((0, 1)), toKiCADPoint((-1, 0)), clearance)

def addHole(board, position, radius):
    circle = pcbnew.PCB_SHAPE()
    circle.SetShape(STROKE_T.S_CIRCLE)
    circle.SetCenter(toKiCADPoint((position[0], position[1])))
    # Set 3'oclock point of the circle to set radius
    circle.SetEnd(toKiCADPoint((position[0], position[1])) + toKiCADPoint((radius/2, 0)))

    circle.SetWidth(radius)
    circle.SetLayer(Layer.F_Paste)
    board.Add(circle)
    addBottomCounterpart(board, circle)

def addJigFrame(board, jigFrameSize, bridgeWidth=fromMm(2),
                bridgeSpacing=fromMm(10), clearance=fromMm(0.5)):
    """
    Given a Pcbnew board finds the board outline and creates a stencil for
    KiKit's stencil jig.

    Mainly, adds mounting holes and mouse bites to define the panel outline.

    jigFrameSize is a tuple (width, height).
    """
    bBox = findBoardBoundingBox(board)
    frameSize = rectByCenter(rectCenter(bBox),
        jigFrameSize[0] + 2 * (OUTER_BORDER + INNER_BORDER),
        jigFrameSize[1] + 2 * (OUTER_BORDER + INNER_BORDER))
    cutSize = rectByCenter(rectCenter(bBox),
        jigFrameSize[0] + 2 * (OUTER_BORDER + INNER_BORDER) - fromMm(1),
        jigFrameSize[1] + 2 * (OUTER_BORDER + INNER_BORDER) - fromMm(1))
    addFrame(board, cutSize, bridgeWidth, bridgeSpacing, clearance)

    for i in range(MOUNTING_HOLES_COUNT):
        x = frameSize.GetX() + OUTER_BORDER / 2 + (i + 1) * (frameSize.GetWidth() - OUTER_BORDER) / (MOUNTING_HOLES_COUNT + 1)
        addHole(board, toKiCADPoint((x, OUTER_BORDER / 2 + frameSize.GetY())), MOUNTING_HOLE_R)
        addHole(board, toKiCADPoint((x, - OUTER_BORDER / 2 +frameSize.GetY() + frameSize.GetHeight())), MOUNTING_HOLE_R)
    for i in range(MOUNTING_HOLES_COUNT):
        y = frameSize.GetY() + OUTER_BORDER / 2 + (i + 1) * (frameSize.GetHeight() - OUTER_BORDER) / (MOUNTING_HOLES_COUNT + 1)
        addHole(board, toKiCADPoint((OUTER_BORDER / 2 + frameSize.GetX(), y)), MOUNTING_HOLE_R)
        addHole(board, toKiCADPoint((- OUTER_BORDER / 2 +frameSize.GetX() + frameSize.GetWidth(), y)), MOUNTING_HOLE_R)

    PIN_TOLERANCE = fromMm(0.05)
    addHole(board, tl(frameSize) + toKiCADPoint((OUTER_BORDER / 2, OUTER_BORDER / 2)), MOUNTING_HOLE_R + PIN_TOLERANCE)
    addHole(board, tr(frameSize) + toKiCADPoint((-OUTER_BORDER / 2, OUTER_BORDER / 2)), MOUNTING_HOLE_R + PIN_TOLERANCE)
    addHole(board, br(frameSize) + toKiCADPoint((-OUTER_BORDER / 2, -OUTER_BORDER / 2)), MOUNTING_HOLE_R + PIN_TOLERANCE)
    addHole(board, bl(frameSize) + toKiCADPoint((OUTER_BORDER / 2, -OUTER_BORDER / 2)), MOUNTING_HOLE_R + PIN_TOLERANCE)
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

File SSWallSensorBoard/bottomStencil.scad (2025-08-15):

// Generated by SolidPython 1.1.3 on 2025-04-28 21:37:47
$fa = 0.4; $fs = 0.4;


rotate(a = 0, v = [1, 0, 0]) {
	difference() {
		scale(v = [1, 1, 1]) {
			difference() {
				linear_extrude(height = 0.9000000000) {
					offset(r = 1.0000000000) {
						import(file = "E:/sourcecode/Micromouseboards/SSWallSensorBoard/SSWallSensorBoard-EdgeCuts.dxf", origin = [0, 0]);
					}
				}
				translate(v = [0, 0, 0.2000000000]) {
					linear_extrude(height = 0.9000000000) {
						translate(v = [0, 0, 0]) {
							import(file = "E:/sourcecode/Micromouseboards/SSWallSensorBoard/SSWallSensorBoard-EdgeCuts.dxf", origin = [0, 0]);
						}
					}
				}
			}
		}
		linear_extrude(center = true, height = 0.8000000000) {
			translate(v = [0, 0, 0]) {
				import(file = "E:/sourcecode/Micromouseboards/SSWallSensorBoard/SSWallSensorBoard-PasteBottom.dxf", origin = [0, 0]);
			}
		}
	}
}
/***********************************************
*********      SolidPython code:      **********
************************************************
 
from pcbnewTransition import pcbnew
import numpy as np
import json
from collections import OrderedDict
from kikit.common import *
from kikit.defs import *
from kikit.substrate import Substrate, extractRings, toShapely, linestringToKicad
from kikit.export import gerberImpl, pasteDxfExport
from kikit.export import exportSettingsJlcpcb
import solid
import solid.utils
import subprocess
import shutil
from kikit.common import removeComponents, parseReferences

from shapely.geometry import Point


OUTER_BORDER = fromMm(7.5)
INNER_BORDER = fromMm(5)
MOUNTING_HOLES_COUNT = 3
MOUNTING_HOLE_R = fromMm(1)
HOLE_SPACING = fromMm(20)

def addBottomCounterpart(board, item):
    item = item.Duplicate()
    item.SetLayer(Layer.B_Paste)
    board.Add(item)

def addRoundedCorner(board, center, start, end, thickness):
    corner = pcbnew.PCB_SHAPE()
    corner.SetShape(STROKE_T.S_ARC)
    corner.SetCenter(toKiCADPoint((center[0], center[1])))
    corner.SetStart(toKiCADPoint((start[0], start[1])))

    if np.cross(start - center, end - center) > 0:
        corner.SetArcAngleAndEnd(fromDegrees(90), True)
    else:
        corner.SetArcAngleAndEnd(fromDegrees(-90), True)
    corner.SetWidth(thickness)
    corner.SetLayer(Layer.F_Paste)
    board.Add(corner)
    addBottomCounterpart(board, corner)

def addLine(board, start, end, thickness):
    line = pcbnew.PCB_SHAPE()
    line.SetShape(STROKE_T.S_SEGMENT)
    line.SetStart(toKiCADPoint((start[0], start[1])))
    line.SetEnd(toKiCADPoint((end[0], end[1])))
    line.SetWidth(thickness)
    line.SetLayer(Layer.F_Paste)
    board.Add(line)
    addBottomCounterpart(board, line)

def addBite(board, origin, direction, normal, thickness):
    """
    Adds a bite to the stencil, direction points to the bridge, normal points
    inside the stencil
    """
    direction = normalize(direction) * thickness
    normal = normalize(normal) * thickness
    center = toKiCADPoint((origin[0], origin[1])) + toKiCADPoint((normal[0], normal[1]))
    start = origin
    end = center + toKiCADPoint((direction[0], direction[1]))
    # addLine(board, end, end + normal / 2, thickness)
    addRoundedCorner(board, center, start, end, thickness)

def numberOfCuts(length, bridgeWidth, bridgeSpacing):
    """
    Return number of bridges which fit inside the length and cut length
    """
    count = int(np.floor((length + bridgeWidth) / (bridgeWidth + bridgeSpacing)))
    cutLength = (length - (count - 1) * bridgeWidth) / count
    return count, cutLength

def addFrame(board, rect, bridgeWidth, bridgeSpacing, clearance):
    """
    Add rectangular frame to the board
    """
    R=fromMm(1)

    corners = [
        (tl(rect), toKiCADPoint((R, 0)), toKiCADPoint((0, R))), # TL
        (tr(rect), toKiCADPoint((0, R)), toKiCADPoint((-R, 0))), # TR
        (br(rect), toKiCADPoint((-R, 0)), toKiCADPoint((0, -R))), # BR
        (bl(rect), toKiCADPoint((0, -R)), toKiCADPoint((R, 0))) # BL
    ]
    for c, sOffset, eOffset in corners:
        addRoundedCorner(board, c + sOffset + eOffset, c + sOffset, c + eOffset, clearance)

    count, cutLength = numberOfCuts(rect.GetWidth() - 2 * R, bridgeWidth, bridgeSpacing)
    for i in range(count):
        start = rect.GetX() + R + i * bridgeWidth + i * cutLength
        end = start + cutLength

        y1, y2 = rect.GetY(), rect.GetY() + rect.GetHeight()
        addLine(board, toKiCADPoint((start, y1)), toKiCADPoint((end, y1)), clearance)
        if i != 0:
            addBite(board, toKiCADPoint((start, y1)), toKiCADPoint((-1, 0)), toKiCADPoint((0, 1)), clearance)
        if i != count - 1:
            addBite(board, toKiCADPoint((end, y1)), toKiCADPoint((1, 0)), toKiCADPoint((0, 1)), clearance)
        addLine(board, toKiCADPoint((start, y2)), toKiCADPoint((end, y2)), clearance)
        if i != 0:
            addBite(board, toKiCADPoint((start, y2)), toKiCADPoint((-1, 0)), toKiCADPoint((0, -1)), clearance)
        if i != count - 1:
            addBite(board, toKiCADPoint((end, y2)), toKiCADPoint((1, 0)), toKiCADPoint((0, -1)), clearance)

    count, cutLength = numberOfCuts(rect.GetHeight() - 2 * R, bridgeWidth, bridgeSpacing)
    for i in range(count):
        start = rect.GetY() + R + i * bridgeWidth + i * cutLength
        end = start + cutLength
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

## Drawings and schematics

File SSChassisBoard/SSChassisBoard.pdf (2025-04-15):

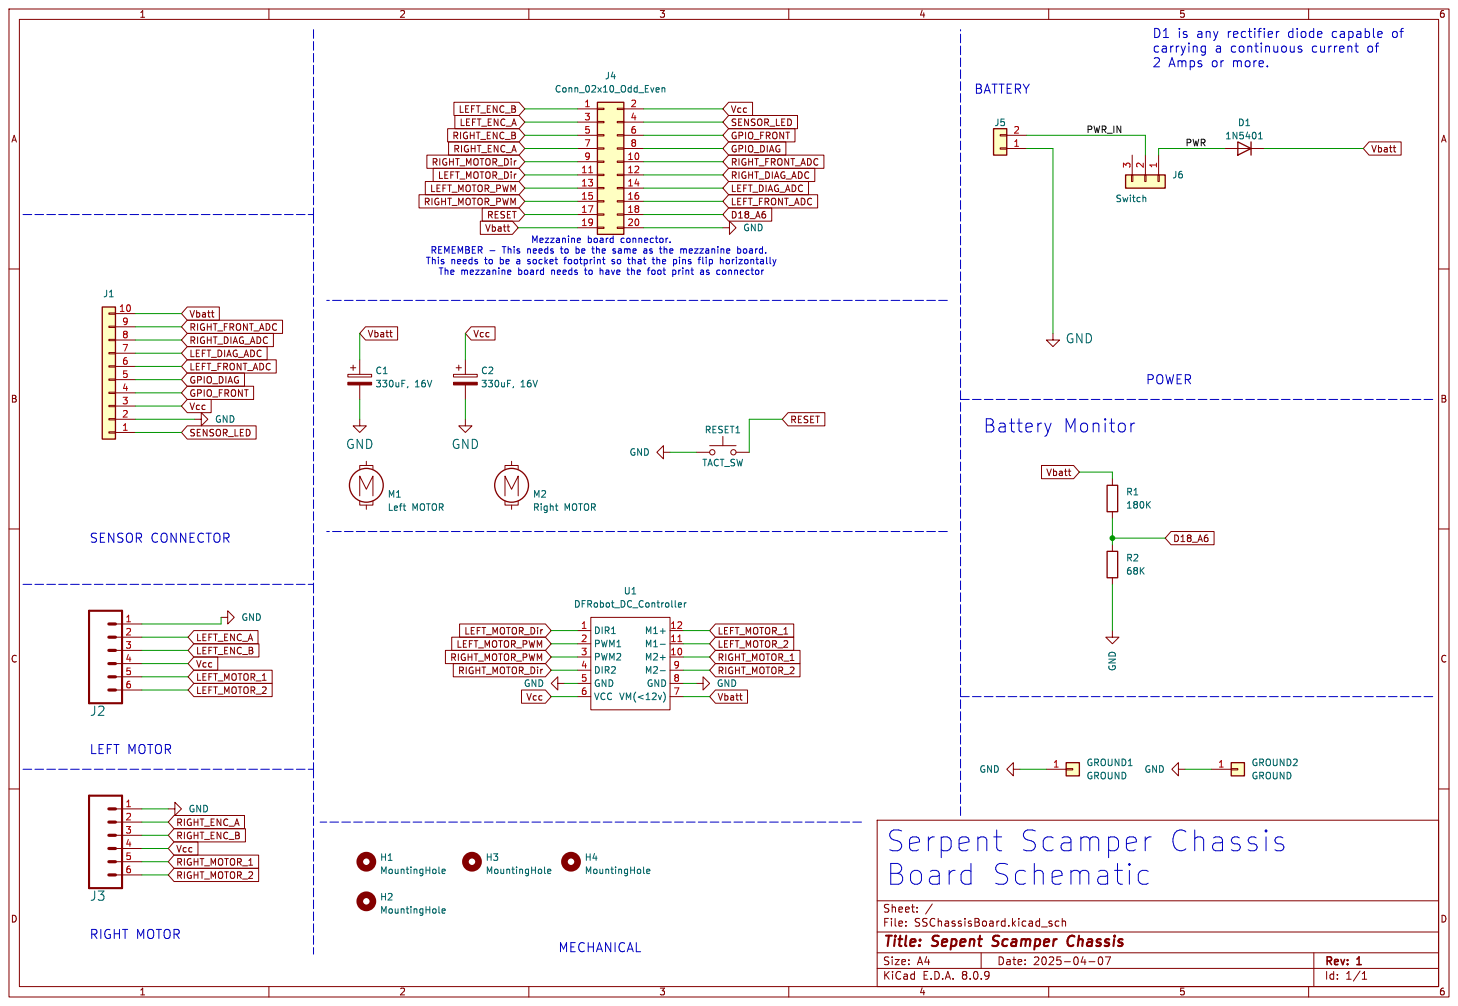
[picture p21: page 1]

2 Amps or more. POWER
1N5401 GND

File: SSChassisBoard.kicad_sch Sheet: / H3 MountingHole

Id: 1/1 Title: Sepent Scamper Chassis

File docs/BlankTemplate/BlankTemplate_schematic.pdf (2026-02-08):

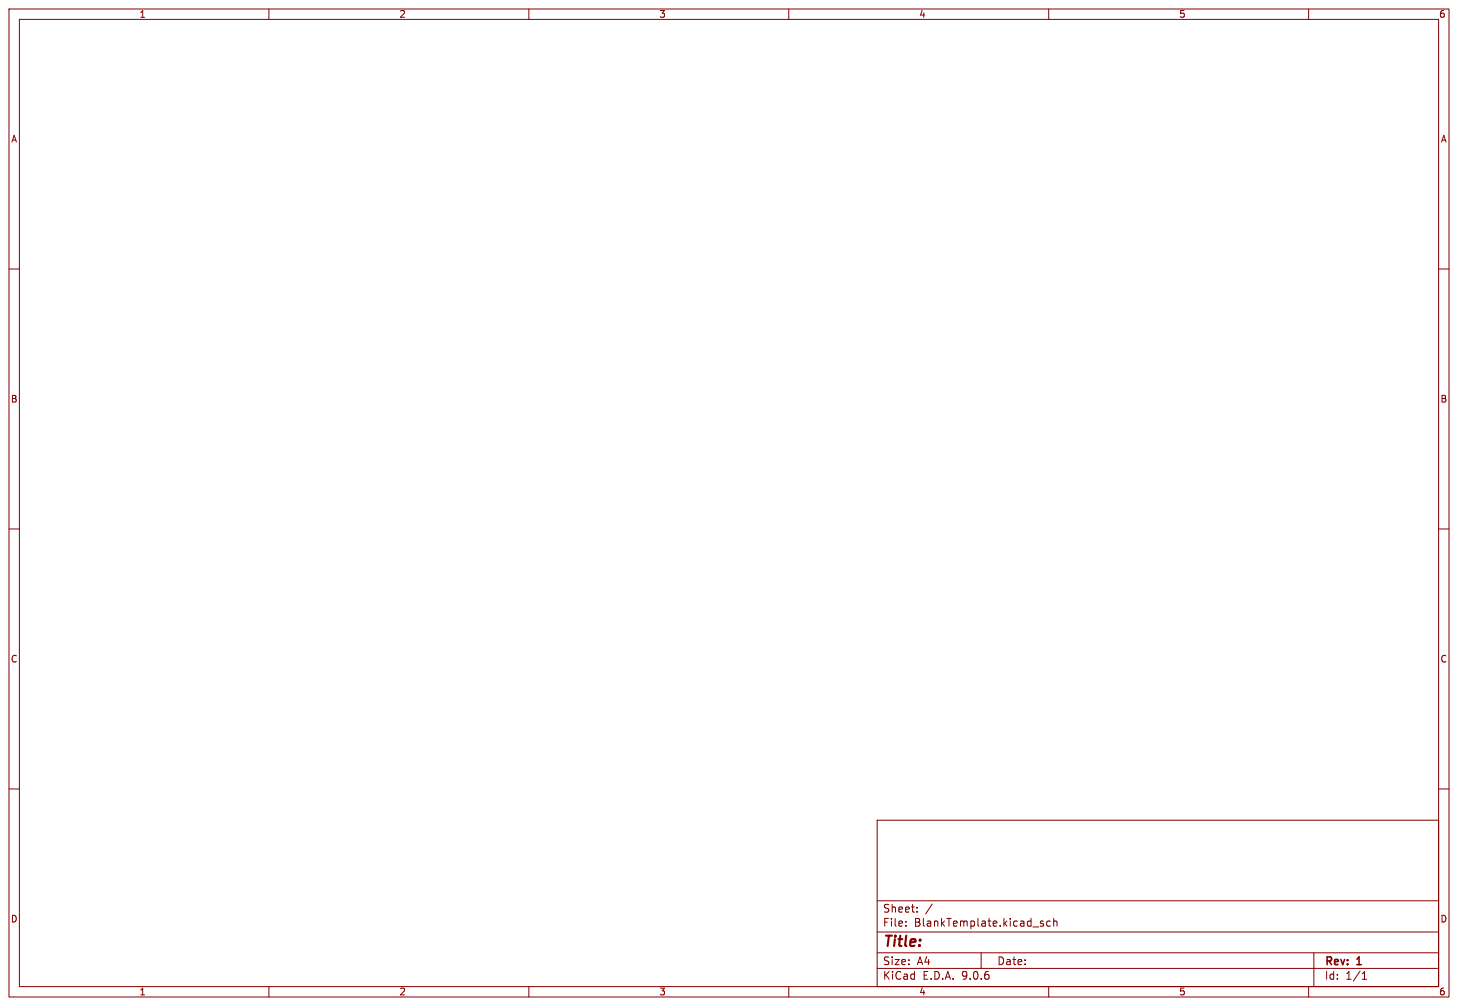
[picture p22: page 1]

Id: 1/1 Title: File: BlankTemplate.kicad_sch Sheet: /

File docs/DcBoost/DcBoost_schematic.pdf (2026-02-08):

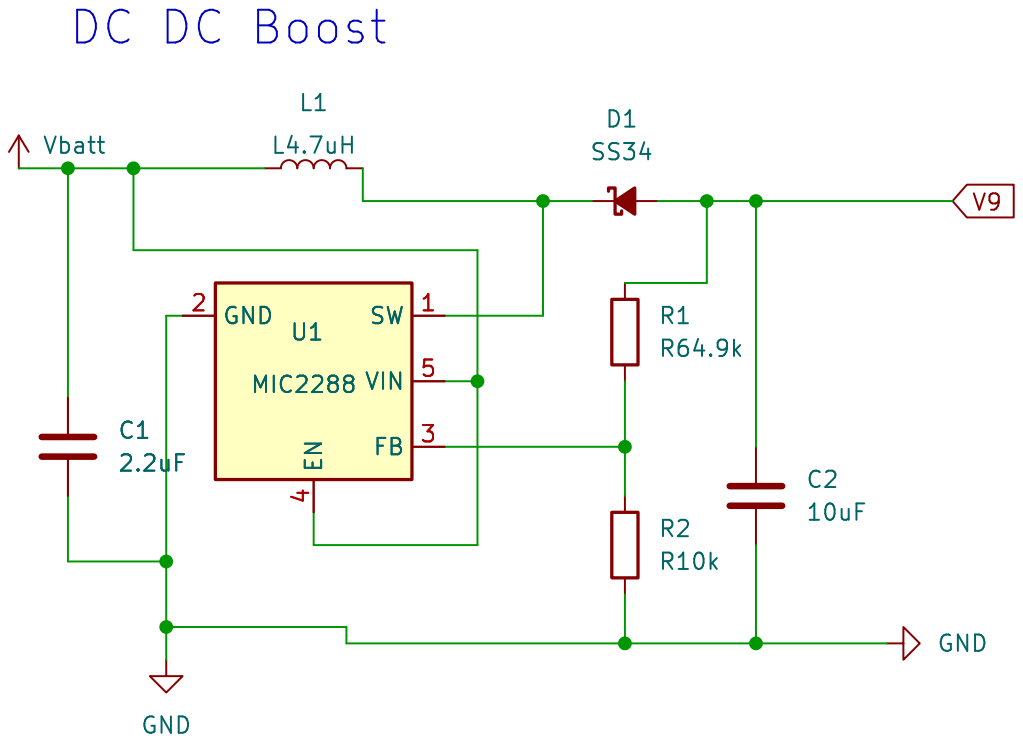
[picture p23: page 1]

4 SW 1 VIN 5 FB 3 U1 MIC2288 R2 R10k V9 DC DC Boost U1 MIC2288 GND 2 EN

Id: 1/1 Title: File: DcBoost.kicad_sch Sheet: /

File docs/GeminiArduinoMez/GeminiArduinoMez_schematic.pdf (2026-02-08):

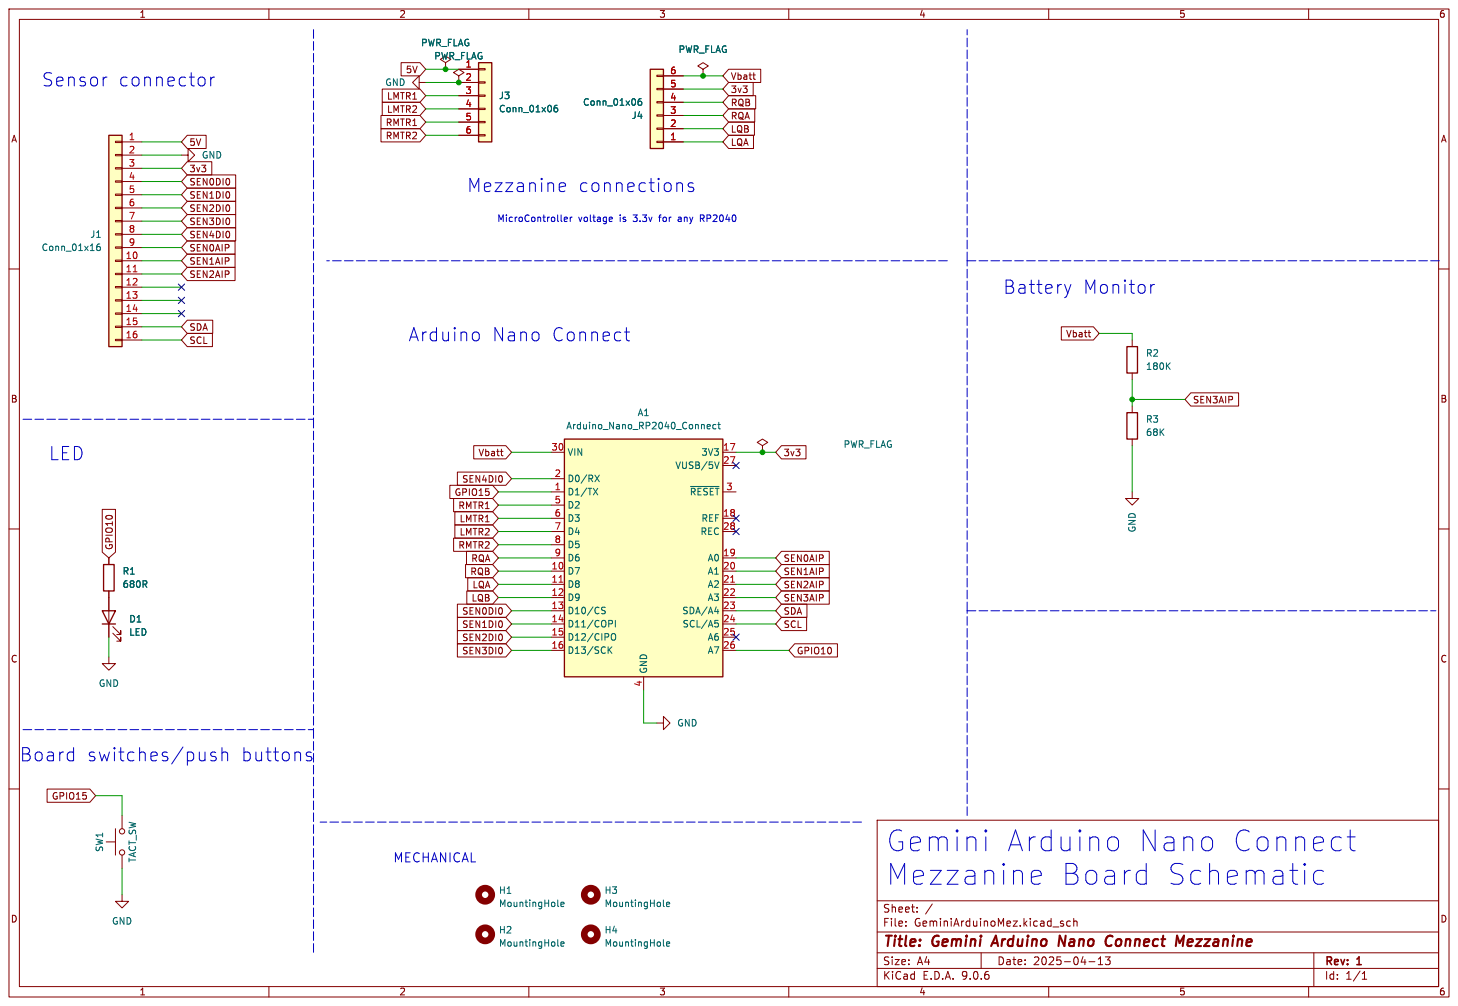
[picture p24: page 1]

Gemini Arduino Nano Connect
Mezzanine Board Schematic

Id: 1/1 Title: Gemini Arduino Nano Connect Mezzanine

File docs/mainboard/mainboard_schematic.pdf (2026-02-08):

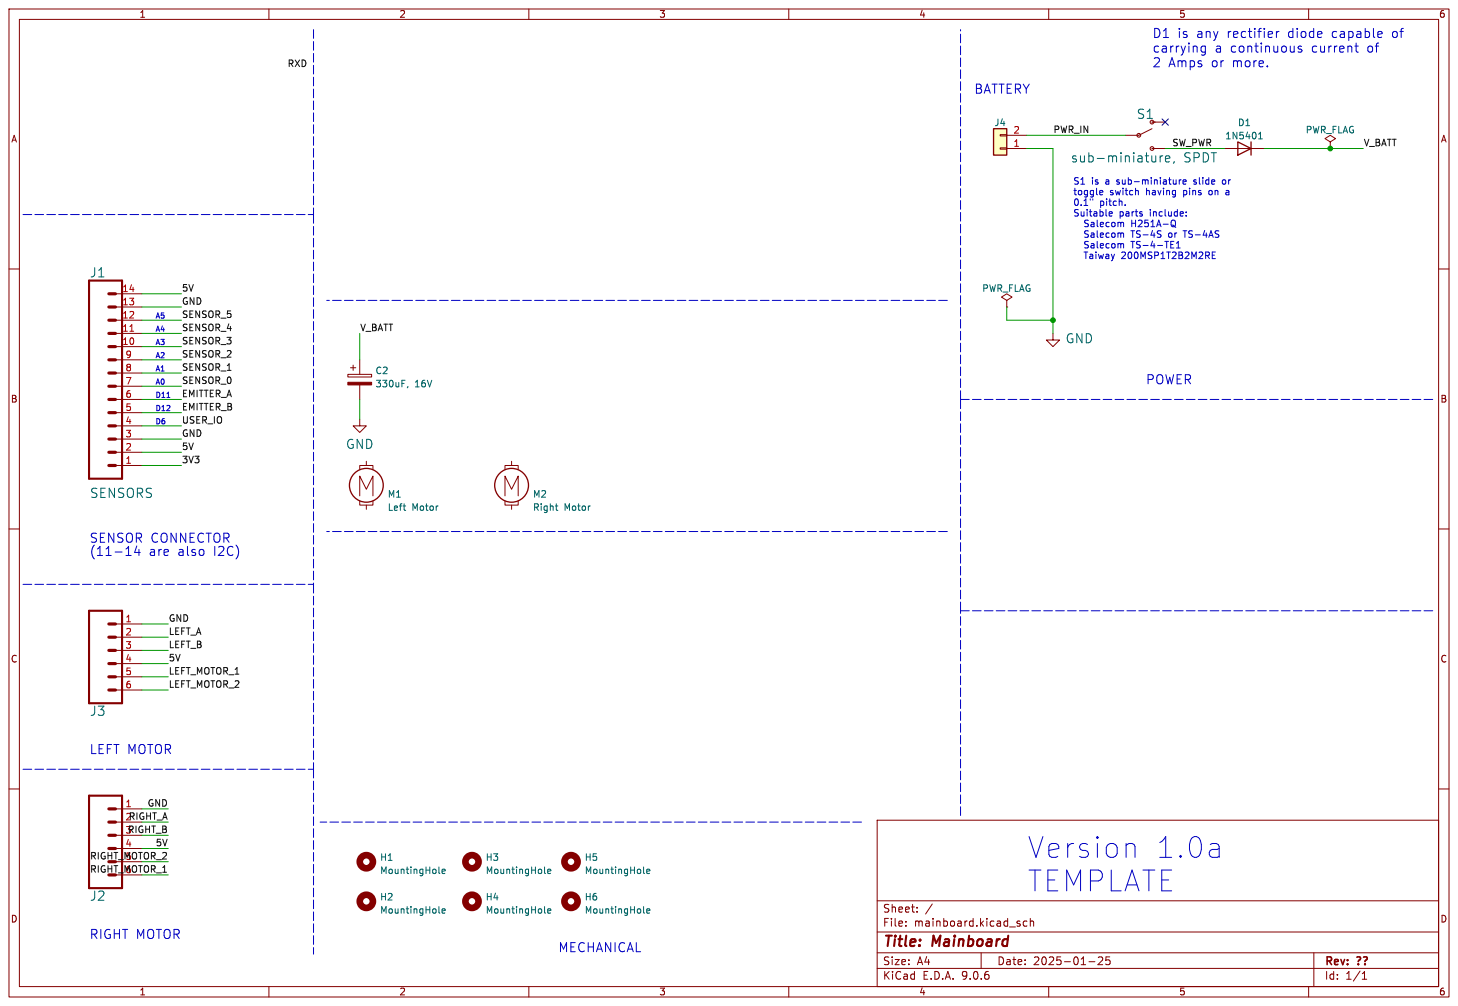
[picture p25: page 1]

2 Amps or more. RIGHT MOTOR

toggle switch having pins on a

Salecom TS-4S or TS-4AS

File: mainboard.kicad_sch Sheet: / H6 MountingHole

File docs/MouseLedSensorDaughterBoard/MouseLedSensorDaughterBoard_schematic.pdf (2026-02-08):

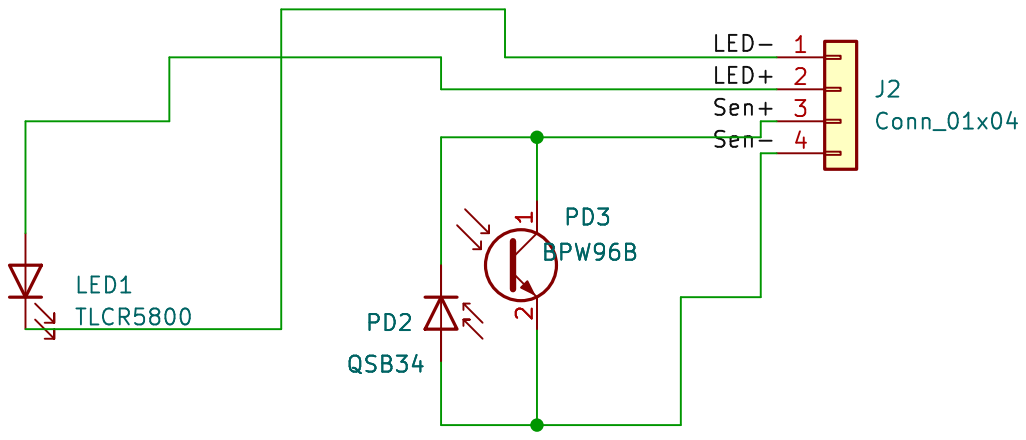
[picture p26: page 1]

Id: 1/1 Title: Mouse SMD Sensor Board

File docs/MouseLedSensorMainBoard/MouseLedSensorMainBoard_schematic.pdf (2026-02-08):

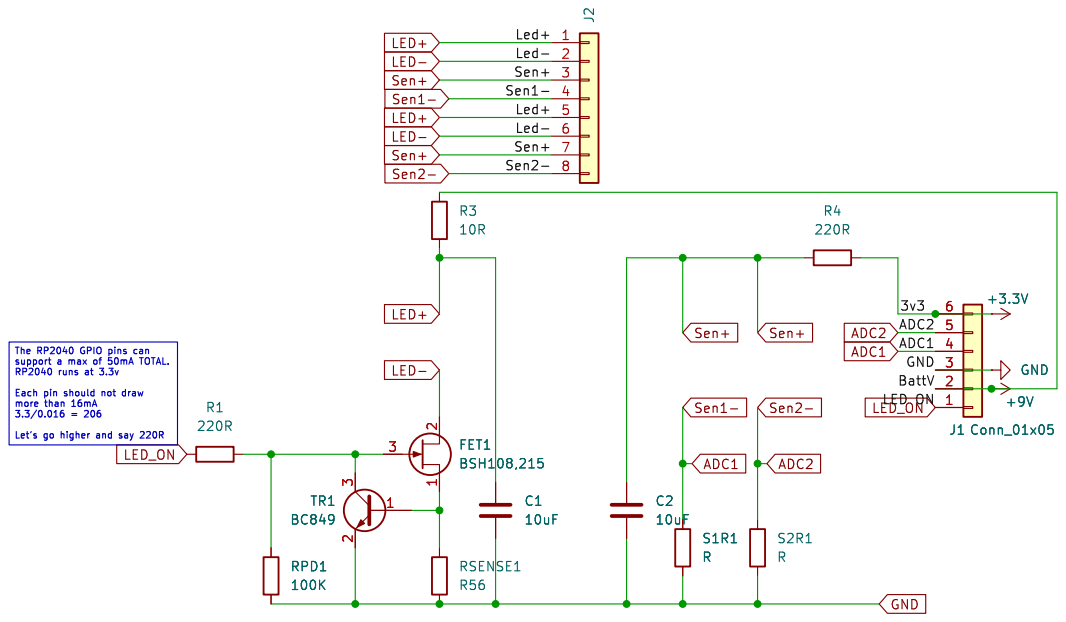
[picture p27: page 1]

The RP2040 GPIO pins can

Id: 1/1 Title: Mouse SMD Sensor Board

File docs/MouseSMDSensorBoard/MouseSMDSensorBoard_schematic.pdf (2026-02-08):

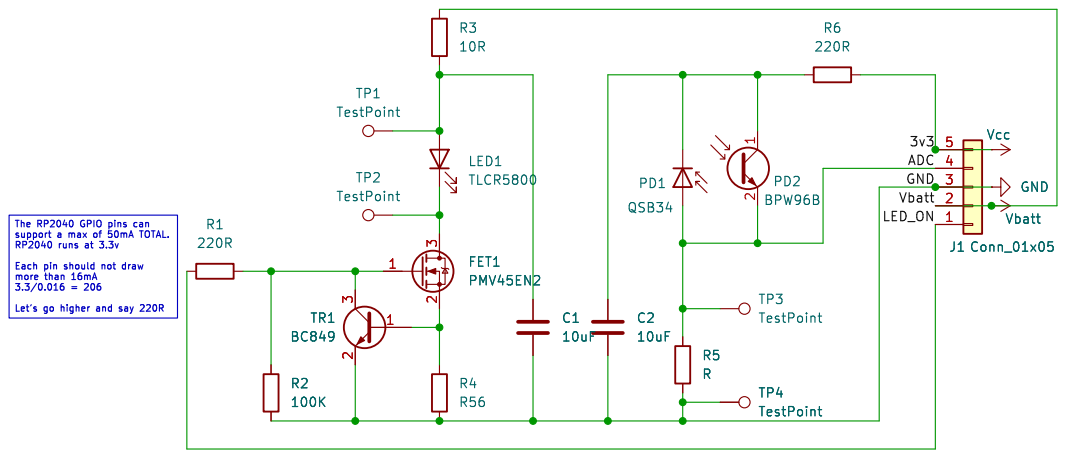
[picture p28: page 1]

The RP2040 GPIO pins can

Id: 1/1 Title: Mouse SMD Sensor Board

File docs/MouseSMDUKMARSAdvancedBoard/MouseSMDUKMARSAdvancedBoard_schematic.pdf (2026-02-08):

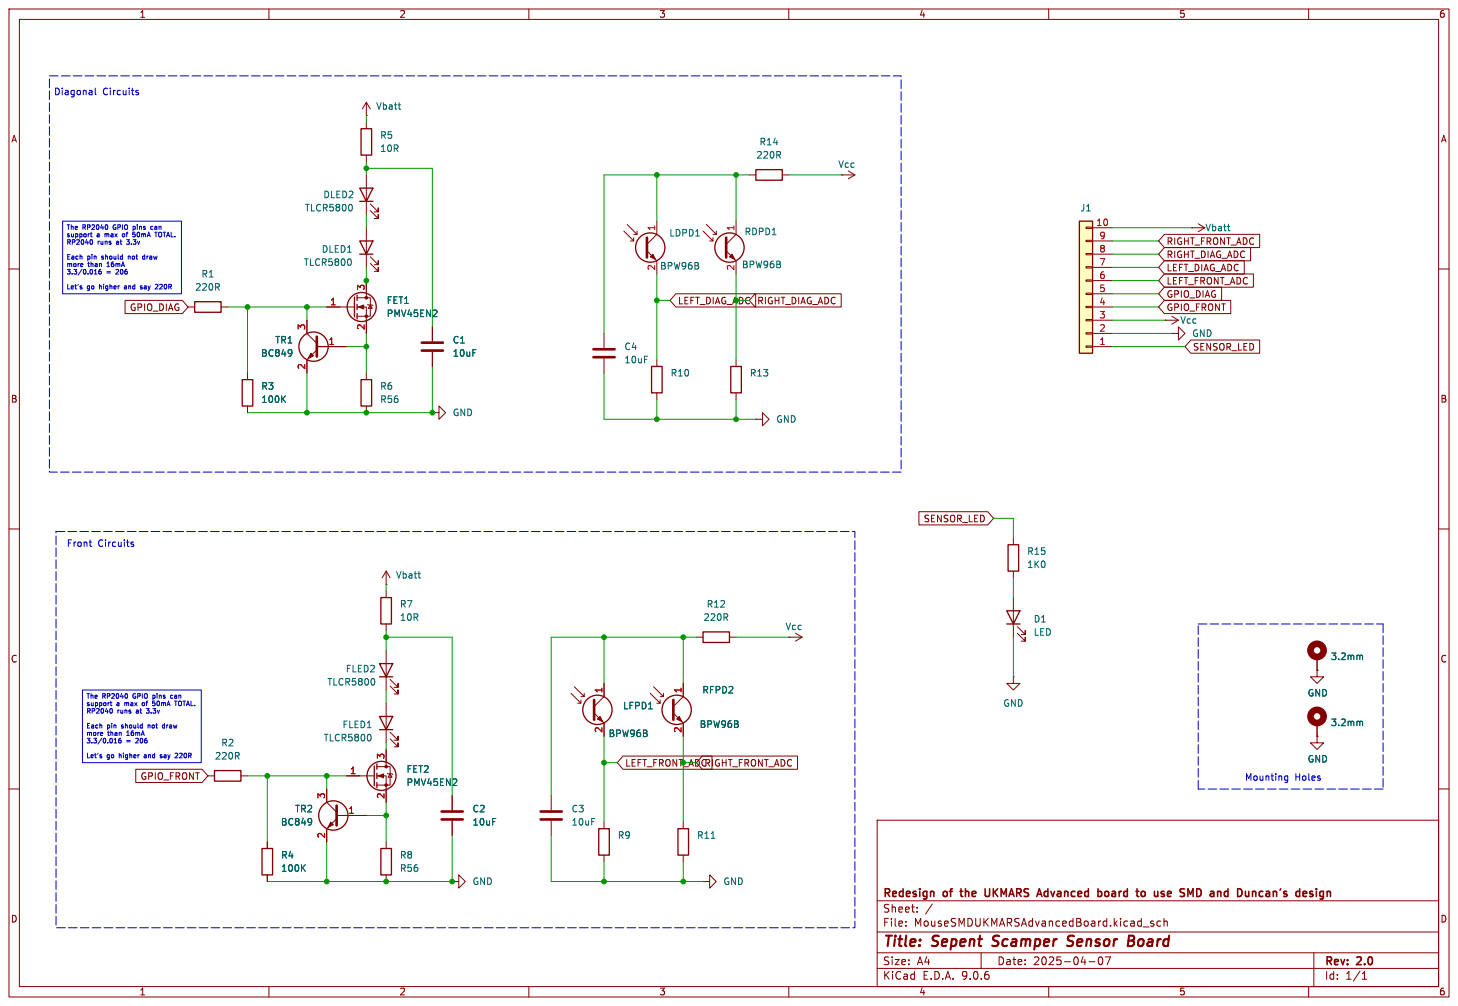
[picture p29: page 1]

The RP2040 GPIO pins can

Let's go higher and say 220R

Id: 1/1 Title: Sepent Scamper Sensor Board

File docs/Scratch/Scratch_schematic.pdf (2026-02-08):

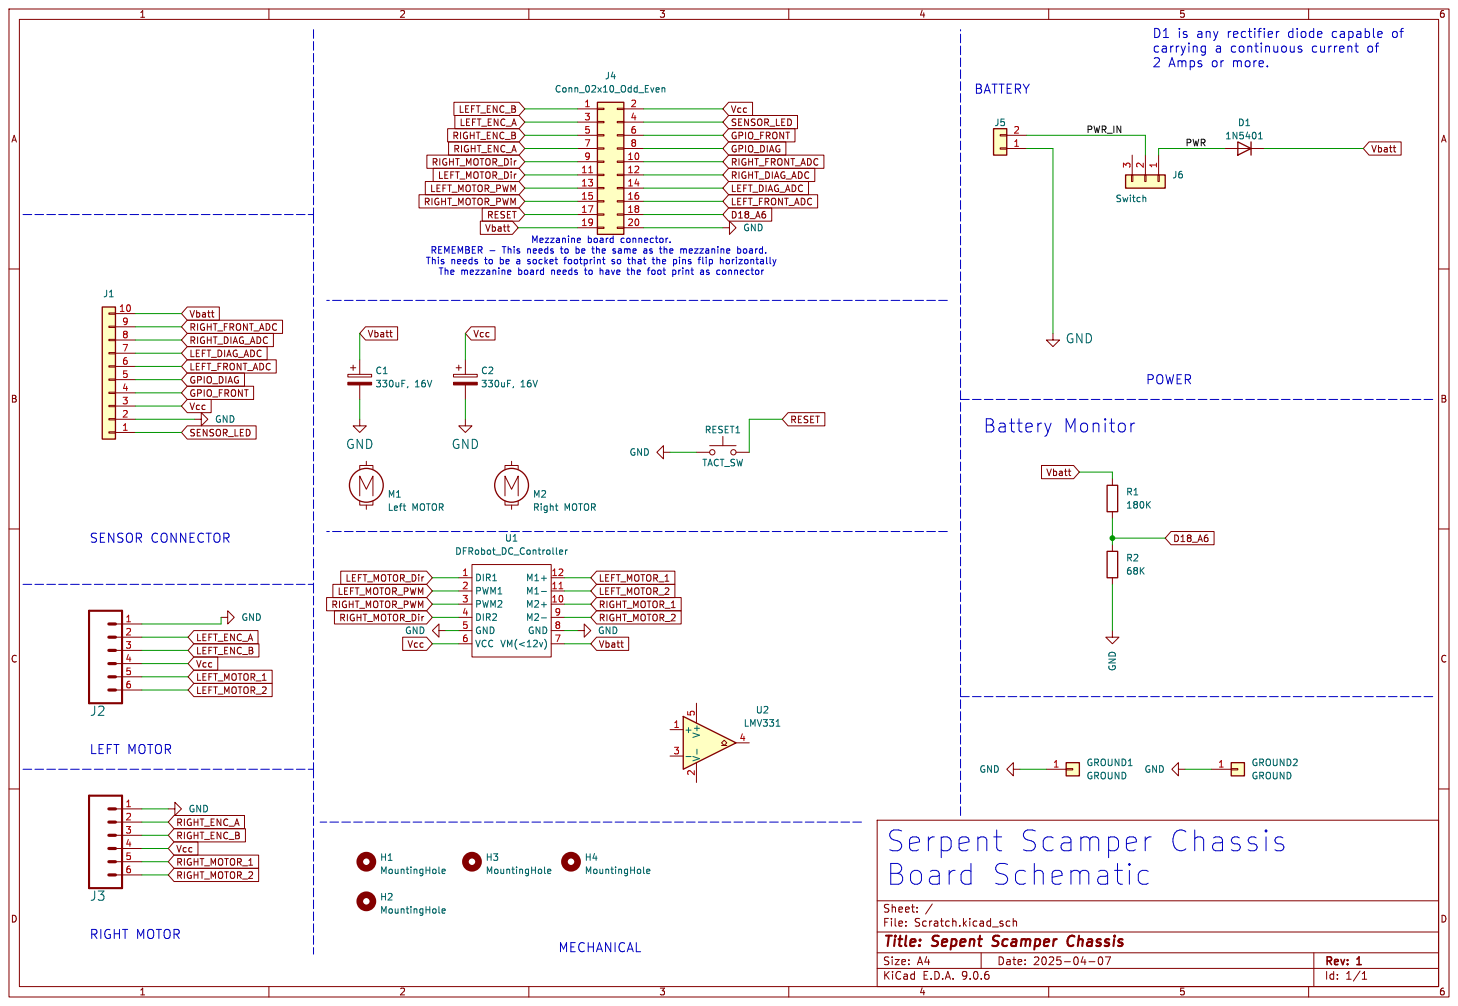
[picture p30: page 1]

2 Amps or more. Serpent Scamper Chassis

Id: 1/1 Title: Sepent Scamper Chassis

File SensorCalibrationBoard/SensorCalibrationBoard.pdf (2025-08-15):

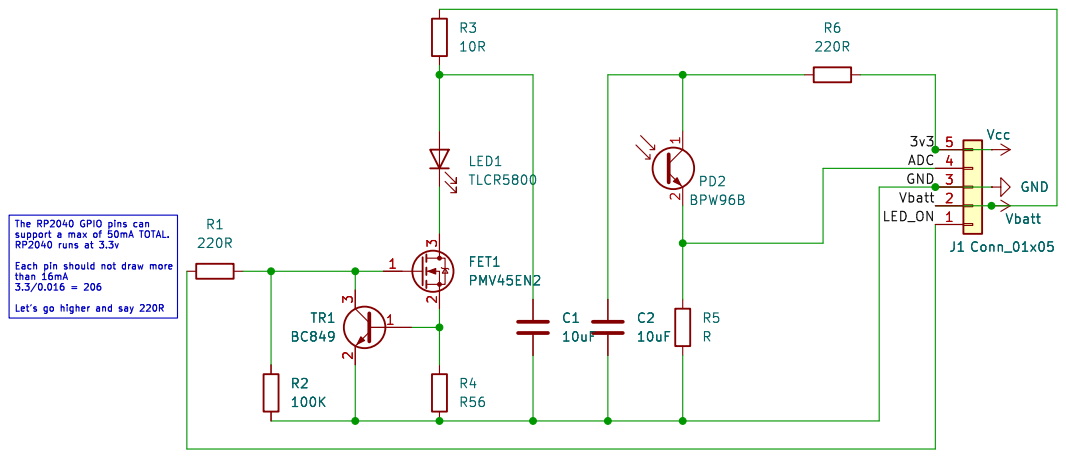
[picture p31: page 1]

The RP2040 GPIO pins can

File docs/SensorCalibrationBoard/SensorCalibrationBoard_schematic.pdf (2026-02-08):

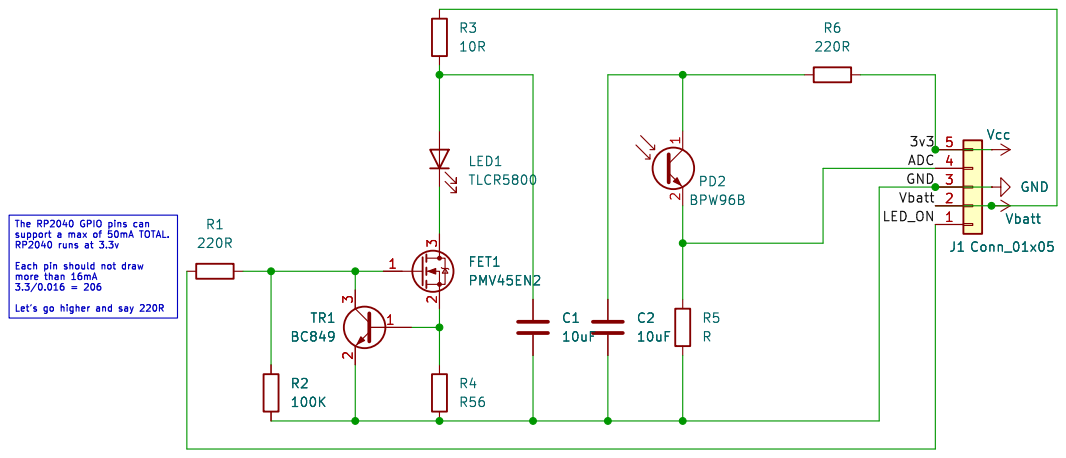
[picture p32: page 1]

The RP2040 GPIO pins can

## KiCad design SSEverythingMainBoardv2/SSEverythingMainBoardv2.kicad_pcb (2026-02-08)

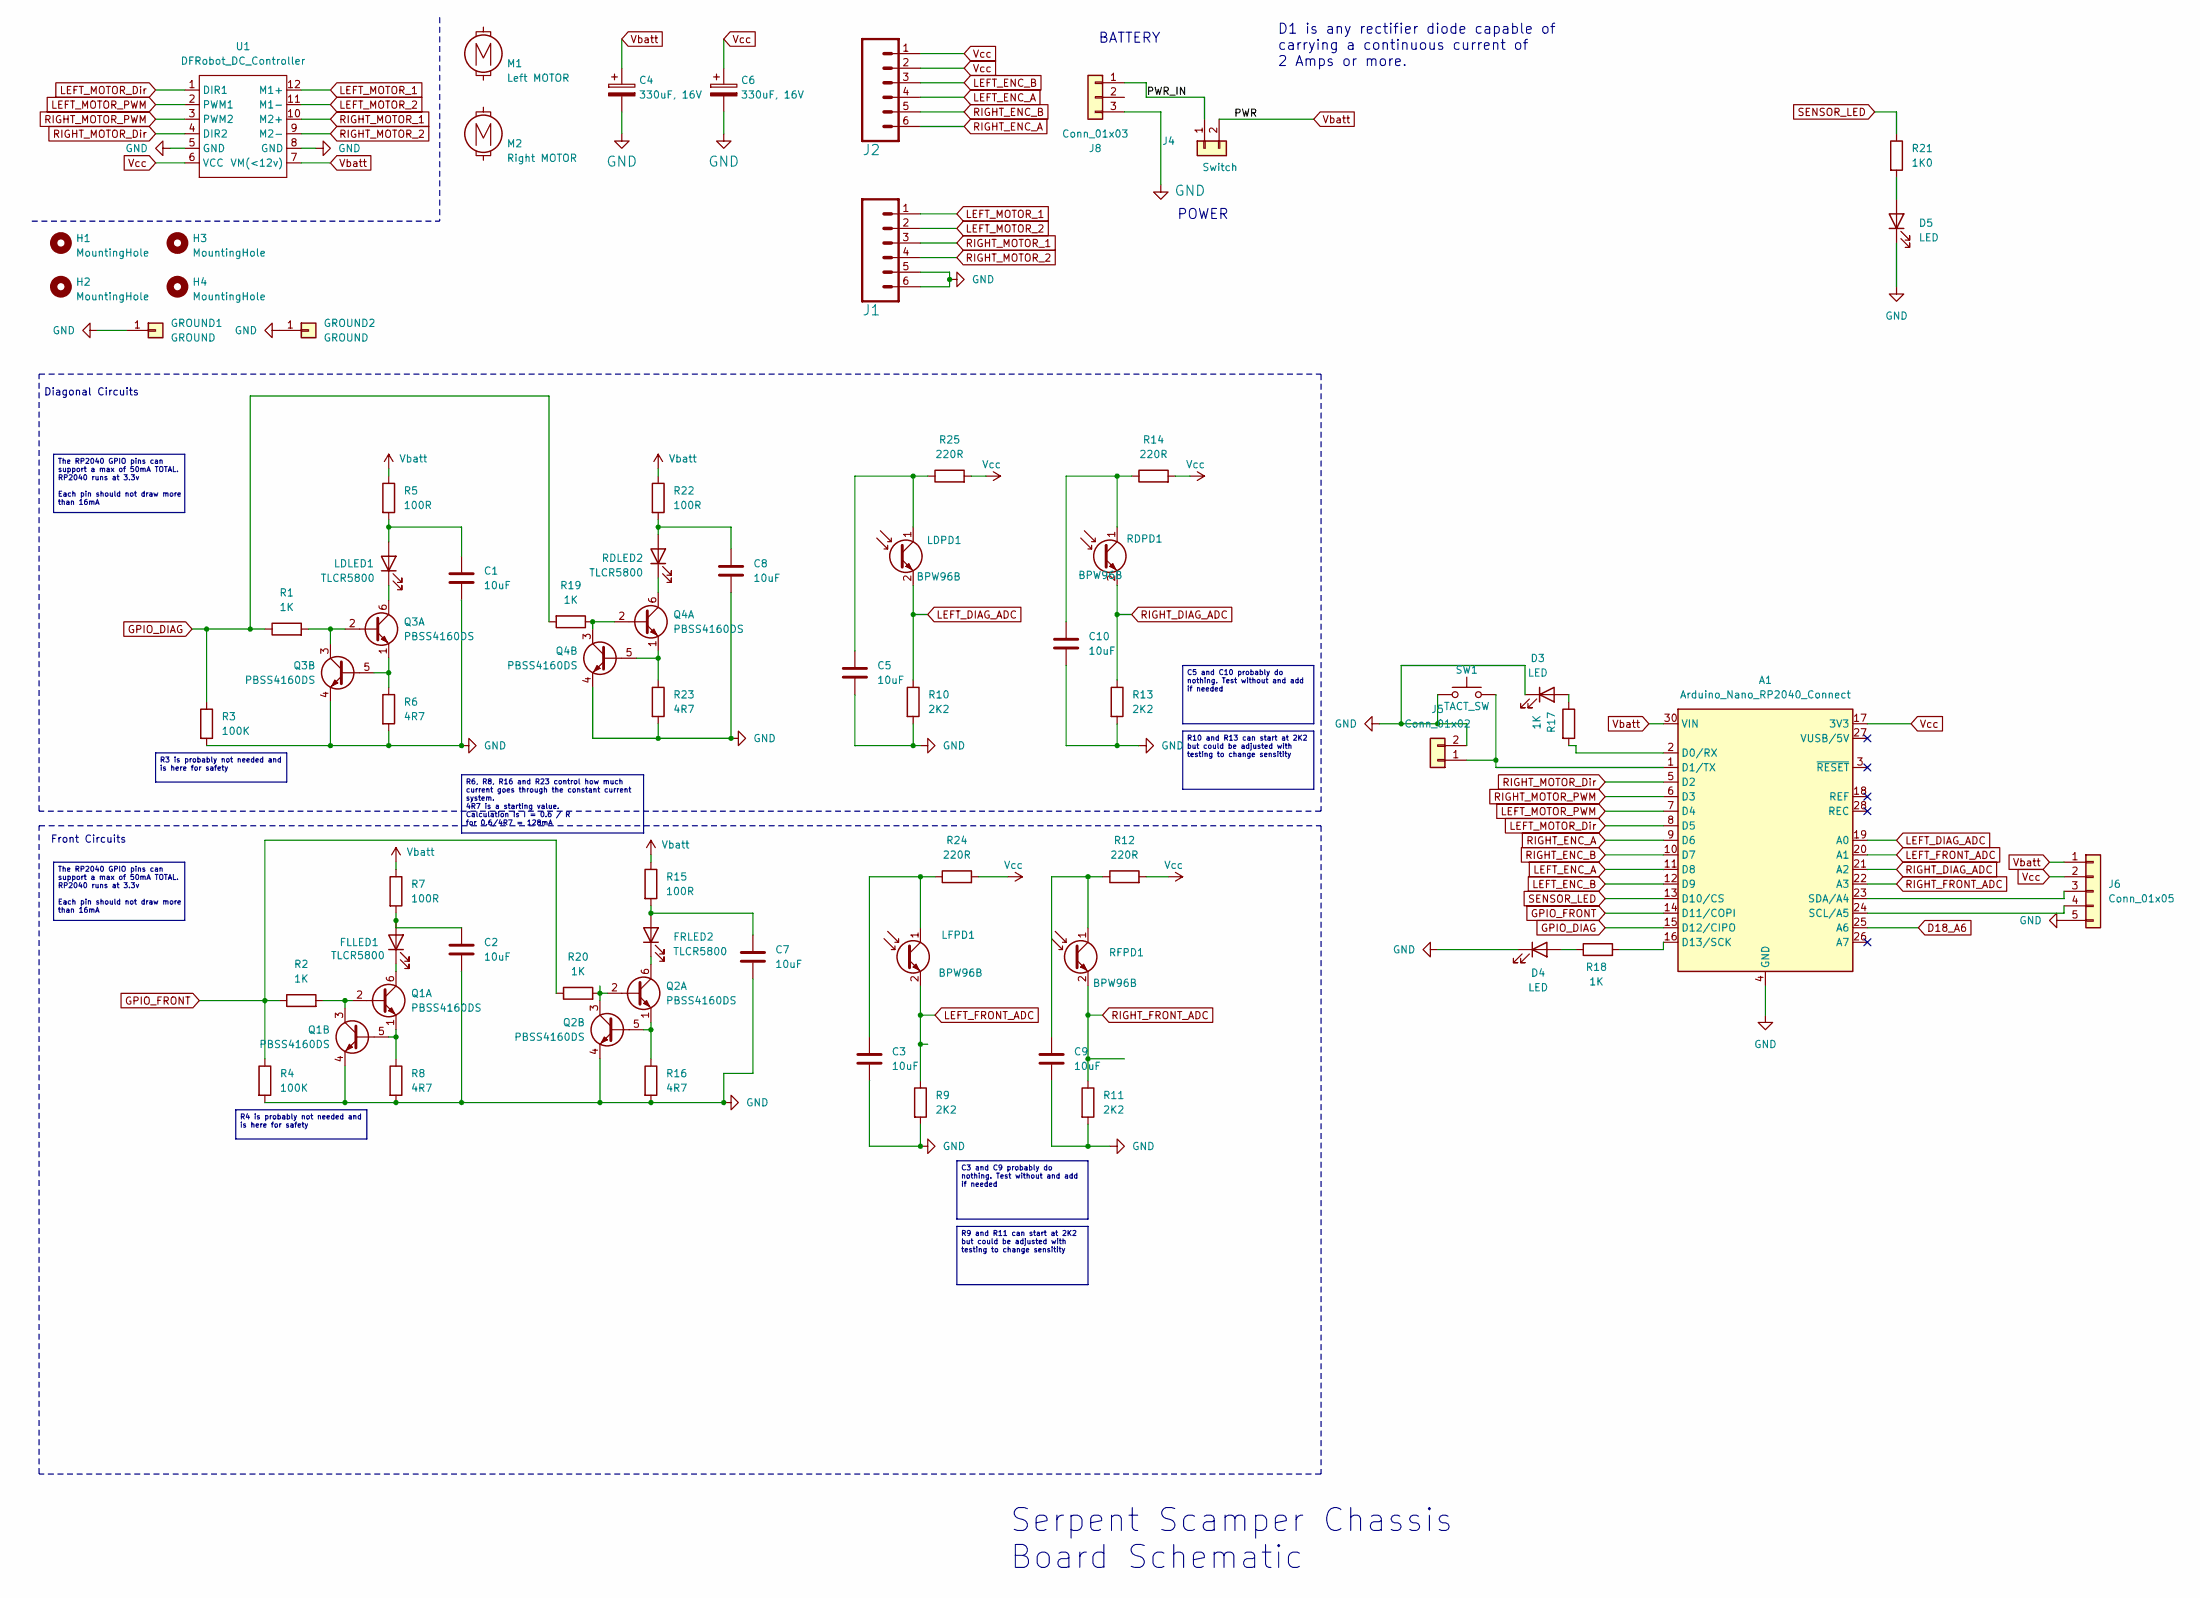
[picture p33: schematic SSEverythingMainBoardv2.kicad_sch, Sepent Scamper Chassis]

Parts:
A1: Arduino_Nano_RP2040_Connect; Arduino_Nano
C1, C2, C3, C5, C7, C8, C9, C10: 10uF; C_1206_3216Metric_Pad1.33x1.80mm_HandSolder
C4, C6: 330uF, 16V; C_Radial_D6.3mm_H7.0mm_P2.50mm
D3, D4, D5: LED; LED_1206_3216Metric_Pad1.42x1.75mm_HandSolder
FLLED1: TLCR5800; LED_D5.0mm_Horizontal_O1.27mm_Z3.0mm
FRLED2: TLCR5800; LED_D5.0mm_Horizontal_O1.27mm_Z3.0mm
GROUND1, GROUND2: GROUND; PinHeader_1x01_P2.54mm_Vertical
H1, H2, H3, H4: MountingHole; MountingHole_3.2mm_M3_clearance
J1, J2: CONN_06SILK_FEMALE_PTH; 1X06_LOCK_LONGPADS
J4: Switch; PinHeader_1x02_P2.54mm_Vertical
J5: Conn_01x02; PinHeader_1x02_P2.54mm_Vertical
J6: Conn_01x05; PinSocket_1x05_P2.54mm_Vertical
J8: Conn_01x03; JST_XH_B3B-XH-A_1x03_P2.50mm_Vertical
LDLED1: TLCR5800; LED_D5.0mm_Horizontal_O1.27mm_Z3.0mm
LDPD1: BPW96B; LED_D5.0mm_Horizontal_O1.27mm_Z3.0mm
LFPD1: BPW96B; LED_D5.0mm_Horizontal_O1.27mm_Z3.0mm
M1: Left MOTOR; MINI-METAL-GEARMOTOR-WITH-BRACKET
M2: Right MOTOR; MINI-METAL-GEARMOTOR-WITH-BRACKET_Alt
Q1, Q2, Q3, Q4: PBSS4160DS; SOT95P275X110-6N
R1, R2, R17, R18, R19, R20: 1K; R_0805_2012Metric_Pad1.20x1.40mm_HandSolder
R3, R4: 100K; R_0805_2012Metric_Pad1.20x1.40mm_HandSolder
R5, R7, R15, R22: 100R; R_0805_2012Metric_Pad1.20x1.40mm_HandSolder
R6, R8, R16, R23: 4R7; R_0805_2012Metric_Pad1.20x1.40mm_HandSolder
R9, R10, R11, R13: 2K2; R_0805_2012Metric_Pad1.20x1.40mm_HandSolder
R12, R14, R24, R25: 220R; R_0805_2012Metric_Pad1.20x1.40mm_HandSolder
R21: 1K0; R_0805_2012Metric_Pad1.20x1.40mm_HandSolder
RDLED2: TLCR5800; LED_D5.0mm_Horizontal_O1.27mm_Z3.0mm
RDPD1: BPW96B; LED_D5.0mm_Horizontal_O1.27mm_Z3.0mm
RFPD1: BPW96B; LED_D5.0mm_Horizontal_O1.27mm_Z3.0mm
SW1: TACT_SW; SW_PUSH_6mm
U1: DFRobot_DC_Controller

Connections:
/PWR_IN: J4.1, J8.1
D18_A6: A1.25 (A6)
GND: A1.4 (GND), A1.29 (GND), C1.1, C2.1, C3.2, C4.2, C5.2, C6.2, C7.1, C8.1, C9.2, C10.2, D3.1 (K), D4.1 (K), D5.1 (K), GROUND1.1, GROUND2.1, J1.5, J1.6, J5.2, J6.5, J8.3, Q1.4 (E2), Q2.4 (E2), Q3.4 (E2), Q4.4 (E2), R3.2, R4.2, R6.2, R8.2, R9.2, R10.2, R11.2, R13.2, R16.2, R23.2, SW1.1 (A), U1.5 (GND), U1.8 (GND)
GPIO_DIAG: A1.15 (D12/CIPO), R1.1, R3.1, R19.2
GPIO_FRONT: A1.14 (D11/COPI), R2.1, R4.1, R20.1
LEFT_DIAG_ADC: A1.19 (A0), LDPD1.2 (E), R10.1
LEFT_ENC_A: A1.11 (D8), J2.4
LEFT_ENC_B: A1.12 (D9), J2.3
LEFT_FRONT_ADC: A1.20 (A1), LFPD1.2 (E), R9.1
LEFT_MOTOR_1: J1.1, U1.12 (M1+)
LEFT_MOTOR_2: J1.2, U1.11 (M1-)
LEFT_MOTOR_Dir: A1.8 (D5), U1.1 (DIR1)
LEFT_MOTOR_PWM: A1.7 (D4), U1.2 (PWM1)
unnamed: A1.2 (D0/RX), R17.2
unnamed: A1.1 (D1/TX), J5.1, SW1.2 (B)
unnamed: A1.16 (D13/SCK), R18.2
unnamed: A1.24 (SCL/A5), J6.4
unnamed: A1.23 (SDA/A4), J6.3
unnamed: D3.2 (A), R17.1
unnamed: D4.2 (A), R18.1
unnamed: D5.2 (A), R21.2
unnamed: C2.2, FLLED1.2 (A), R7.2
unnamed: FLLED1.1 (K), Q1.6 (C1)
unnamed: C7.2, FRLED2.2 (A), R15.2
unnamed: FRLED2.1 (K), Q2.6 (C1)
unnamed: C1.2, LDLED1.2 (A), R5.2
unnamed: LDLED1.1 (K), Q3.6 (C1)
unnamed: C5.1, LDPD1.1 (C), R25.1
unnamed: C3.1, LFPD1.1 (C), R24.1
unnamed: Q1.2 (B1), Q1.3 (C2), R2.2
unnamed: Q1.1 (E1), Q1.5 (B2), R8.1
unnamed: Q2.2 (B1), Q2.3 (C2), R20.2
unnamed: Q2.1 (E1), Q2.5 (B2), R16.1
unnamed: Q3.2 (B1), Q3.3 (C2), R1.2
unnamed: Q3.1 (E1), Q3.5 (B2), R6.1
unnamed: Q4.2 (B1), Q4.3 (C2), R19.1
unnamed: Q4.6 (C1), RDLED2.1 (K)
unnamed: Q4.1 (E1), Q4.5 (B2), R23.1
unnamed: C8.2, R22.2, RDLED2.2 (A)
unnamed: C10.1, R14.1, RDPD1.1 (C)
unnamed: C9.1, R12.1, RFPD1.1 (C)
RIGHT_DIAG_ADC: A1.21 (A2), R13.1, RDPD1.2 (E)
RIGHT_ENC_A: A1.9 (D6), J2.6
RIGHT_ENC_B: A1.10 (D7), J2.5
RIGHT_FRONT_ADC: A1.22 (A3), R11.1, RFPD1.2 (E)
RIGHT_MOTOR_1: J1.3, U1.10 (M2+)
RIGHT_MOTOR_2: J1.4, U1.9 (M2-)
RIGHT_MOTOR_Dir: A1.5 (D2), U1.4 (DIR2)
RIGHT_MOTOR_PWM: A1.6 (D3), U1.3 (PWM2)
SENSOR_LED: A1.13 (D10/CS), R21.1
Vbatt: A1.30 (VIN), C4.1, J4.2, J6.1, R5.1, R7.1, R15.1, R22.1, U1.7 (VM(<12v))
Vcc: A1.17 (3V3), C6.1, J2.1, J2.2, J6.2, R12.2, R14.2, R24.2, R25.2, U1.6 (VCC)

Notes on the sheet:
D1 is any rectifier diode capable of carrying a continuous current of 2 Amps or more.
Front Circuits
POWER
Diagonal Circuits
BATTERY
Serpent Scamper Chassis Board Schematic
R10 and R13 can start at 2K2 but could be adjusted with testing to change sensitity
C3 and C9 probably do nothing. Test without and add if needed
R3 is probably not needed and is here for safety
R6, R8, R16 and R23 control how much current goes through the constant current system. 4R7 is a starting value. Calculation is I = 0.6 / R for 0.6/4R7 = 128mA
C5 and C10 probably do nothing. Test without and add if needed
The RP2040 GPIO pins can support a max of 50mA TOTAL. RP2040 runs at 3.3v Each pin should not draw more than 16mA
R4 is probably not needed and is here for safety
R9 and R11 can start at 2K2 but could be adjusted with testing to change sensitity

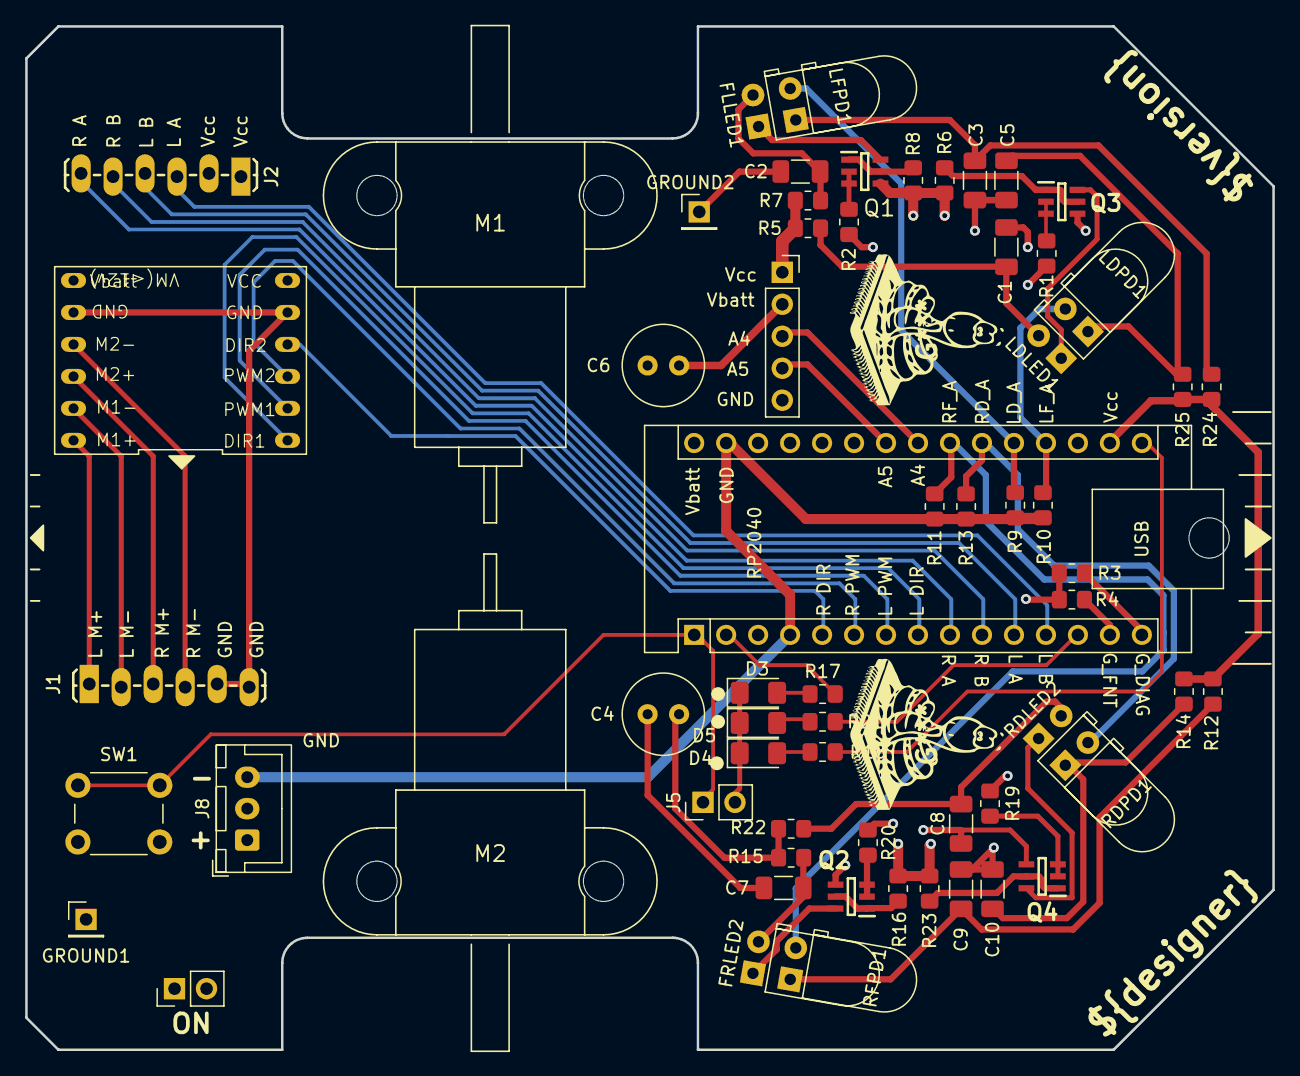
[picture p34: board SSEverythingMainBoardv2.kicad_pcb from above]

Board: 4 copper layers, 99.1 x 81.3 mm, 67 parts (0 on the bottom side), 51 nets.

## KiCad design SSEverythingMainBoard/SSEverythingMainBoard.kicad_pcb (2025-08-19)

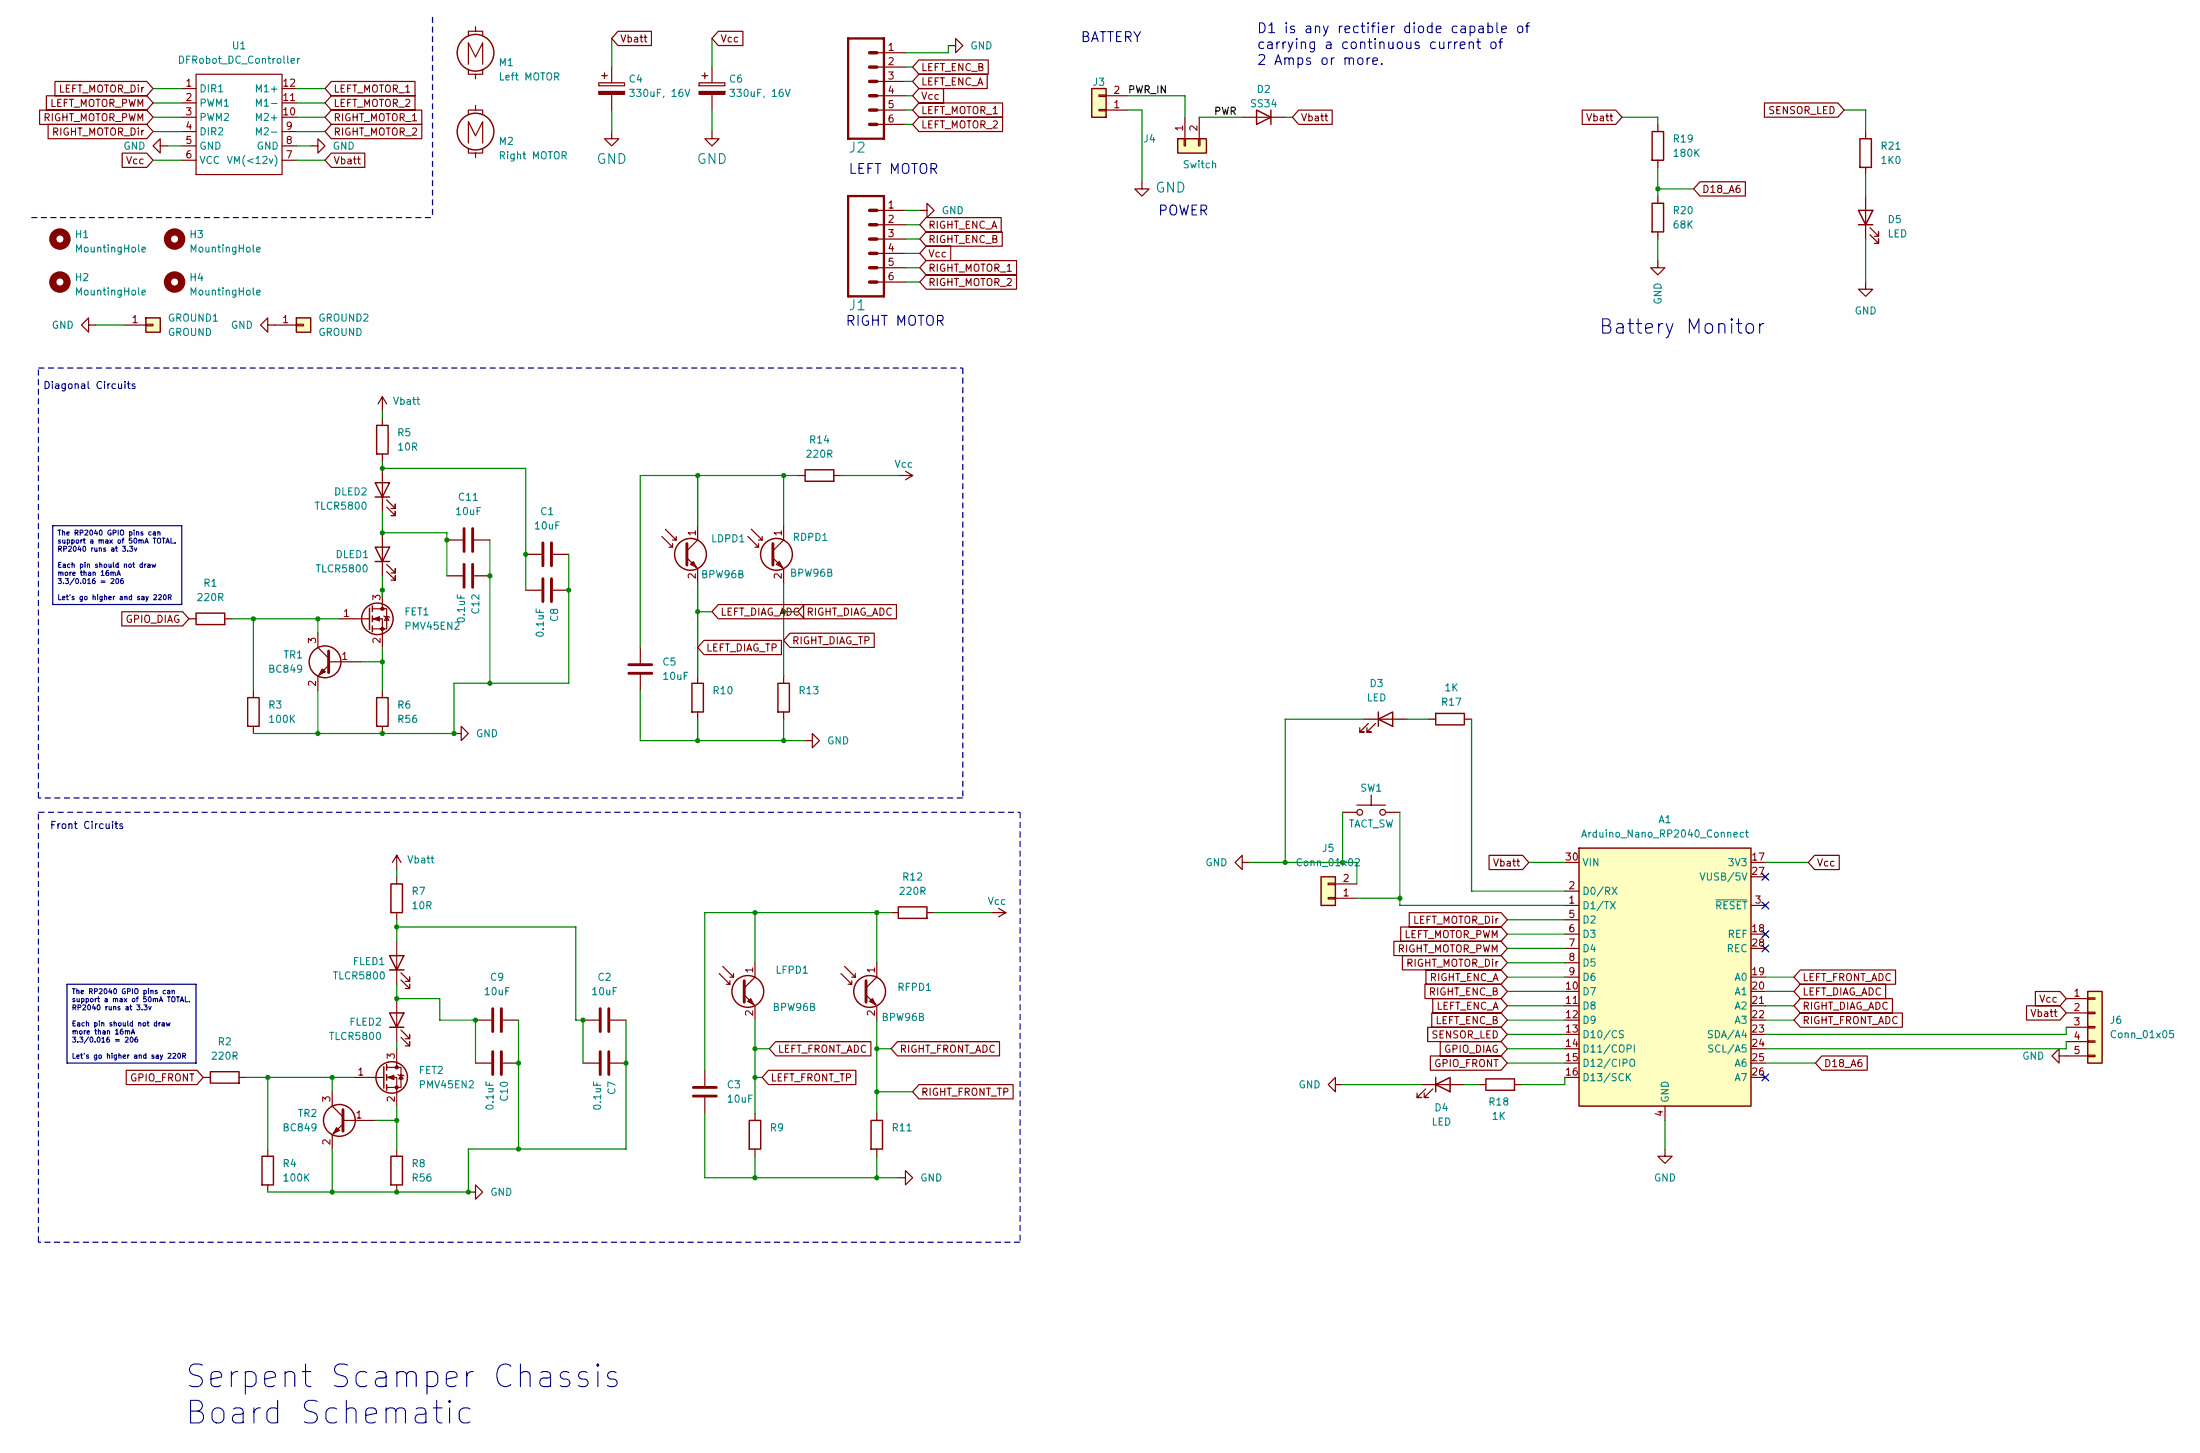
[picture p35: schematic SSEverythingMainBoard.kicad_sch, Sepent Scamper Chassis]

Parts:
A1: Arduino_Nano_RP2040_Connect; Arduino_Nano
C1, C2, C3, C5, C9, C11: 10uF; C_0805_2012Metric_Pad1.18x1.45mm_HandSolder
C4, C6: 330uF, 16V; CP_Radial_D8.0mm_P2.50mm
C7, C8, C10, C12: 0.1uF; C_0805_2012Metric_Pad1.18x1.45mm_HandSolder
D2: SS34; D_SMC
D3, D4, D5: LED; LED_1206_3216Metric_Pad1.42x1.75mm_HandSolder
DLED1, DLED2: TLCR5800; LED_D5.0mm_Horizontal_O1.27mm_Z3.0mm
FET1, FET2: PMV45EN2; SOT-23_Handsoldering
FLED1, FLED2: TLCR5800; LED_D5.0mm_Horizontal_O1.27mm_Z3.0mm
GROUND1, GROUND2: GROUND; PinHeader_1x01_P2.54mm_Vertical
H1, H2, H3, H4: MountingHole; MountingHole_3.2mm_M3_clearance
J1, J2: CONN_06SILK_FEMALE_PTH; 1X06_LOCK_LONGPADS
J3: POWER; PinHeader_1x02_P2.54mm_Vertical
J4: Switch; PinHeader_1x02_P2.54mm_Vertical
J5: Conn_01x02; PinHeader_1x02_P2.54mm_Vertical
J6: Conn_01x05; PinSocket_1x05_P2.54mm_Vertical
LDPD1: BPW96B; LED_D5.0mm_Horizontal_O1.27mm_Z3.0mm
LFPD1: BPW96B; LED_D5.0mm_Horizontal_O1.27mm_Z3.0mm
M1: Left MOTOR; MINI-METAL-GEARMOTOR-WITH-BRACKET_Alt
M2: Right MOTOR; MINI-METAL-GEARMOTOR-WITH-BRACKET
R1, R2, R12, R14: 220R; R_0805_2012Metric_Pad1.20x1.40mm_HandSolder
R3, R4: 100K; R_0805_2012Metric_Pad1.20x1.40mm_HandSolder
R5, R7: 10R; R_0805_2012Metric_Pad1.20x1.40mm_HandSolder
R6, R8: R56; R_0805_2012Metric_Pad1.20x1.40mm_HandSolder
R9, R10, R11, R13: R; R_0805_2012Metric_Pad1.20x1.40mm_HandSolder
R17, R18: 1K; R_0805_2012Metric_Pad1.20x1.40mm_HandSolder
R19: 180K; R_0805_2012Metric_Pad1.20x1.40mm_HandSolder
R20: 68K; R_0805_2012Metric_Pad1.20x1.40mm_HandSolder
R21: 1K0; R_0805_2012Metric_Pad1.20x1.40mm_HandSolder
RDPD1: BPW96B; LED_D5.0mm_Horizontal_O1.27mm_Z3.0mm
RFPD1: BPW96B; LED_D5.0mm_Horizontal_O1.27mm_Z3.0mm
SW1: TACT_SW; SW_PUSH_6mm
TR1, TR2: BC849; SOT-23_Handsoldering
U1: DFRobot_DC_Controller

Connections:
/PWR: D2.2 (A), J4.2
/PWR_IN: J3.2, J4.1
D18_A6: A1.25 (A6), R19.2, R20.1
GND: A1.4 (GND), A1.29 (GND), C1.2, C2.2, C3.2, C4.2, C5.2, C6.2, C7.1, C8.1, C9.2, C10.1, C11.2, C12.1, D3.1 (K), D4.1 (K), D5.1 (K), GROUND1.1, GROUND2.1, J1.1, J2.1, J3.1, J5.2, J6.5, R3.2, R4.2, R6.2, R8.2, R9.2, R10.2, R11.2, R13.2, R20.2, SW1.1 (A), TR1.2 (E), TR2.2 (E), U1.5 (GND), U1.8 (GND)
GPIO_DIAG: A1.14 (D11/COPI), R1.1
GPIO_FRONT: A1.15 (D12/CIPO), R2.1
LEFT_DIAG_ADC: A1.20 (A1), LDPD1.2 (E), R10.1
LEFT_ENC_A: A1.11 (D8), J2.3
LEFT_ENC_B: A1.12 (D9), J2.2
LEFT_FRONT_ADC: A1.19 (A0), LFPD1.2 (E), R9.1
LEFT_MOTOR_1: J2.5, U1.12 (M1+)
LEFT_MOTOR_2: J2.6, U1.11 (M1-)
LEFT_MOTOR_Dir: A1.5 (D2), U1.1 (DIR1)
LEFT_MOTOR_PWM: A1.6 (D3), U1.2 (PWM1)
unnamed: A1.2 (D0/RX), R17.1
unnamed: A1.1 (D1/TX), J5.1, SW1.2 (B)
unnamed: A1.16 (D13/SCK), R18.2
unnamed: A1.24 (SCL/A5), J6.4
unnamed: A1.23 (SDA/A4), J6.3
unnamed: D3.2 (A), R17.2
unnamed: D4.2 (A), R18.1
unnamed: D5.2 (A), R21.2
unnamed: C11.1, C12.2, DLED1.2 (A), DLED2.1 (K)
unnamed: DLED1.1 (K), FET1.3 (D)
unnamed: C1.1, C8.2, DLED2.2 (A), R5.2
unnamed: FET1.1 (G), R1.2, R3.1, TR1.3 (C)
unnamed: FET1.2 (S), R6.1, TR1.1 (B)
unnamed: FET2.3 (D), FLED2.1 (K)
unnamed: FET2.1 (G), R2.2, R4.1, TR2.3 (C)
unnamed: FET2.2 (S), R8.1, TR2.1 (B)
unnamed: C2.1, C7.2, FLED1.2 (A), R7.2
unnamed: C9.1, C10.2, FLED1.1 (K), FLED2.2 (A)
unnamed: C5.1, LDPD1.1 (C), R14.1, RDPD1.1 (C)
unnamed: C3.1, LFPD1.1 (C), R12.1, RFPD1.1 (C)
RIGHT_DIAG_ADC: A1.21 (A2), R13.1, RDPD1.2 (E)
RIGHT_ENC_A: A1.9 (D6), J1.2
RIGHT_ENC_B: A1.10 (D7), J1.3
RIGHT_FRONT_ADC: A1.22 (A3), R11.1, RFPD1.2 (E)
RIGHT_MOTOR_1: J1.5, U1.10 (M2+)
RIGHT_MOTOR_2: J1.6, U1.9 (M2-)
RIGHT_MOTOR_Dir: A1.8 (D5), U1.4 (DIR2)
RIGHT_MOTOR_PWM: A1.7 (D4), U1.3 (PWM2)
SENSOR_LED: A1.13 (D10/CS), R21.1
Vbatt: A1.30 (VIN), C4.1, D2.1 (K), J6.2, R5.1, R7.1, R19.1, U1.7 (VM(<12v))
Vcc: A1.17 (3V3), C6.1, J1.4, J2.4, J6.1, R12.2, R14.2, U1.6 (VCC)

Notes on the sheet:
The RP2040 GPIO pins can support a max of 50mA TOTAL. RP2040 runs at 3.3v Each pin should not draw more than 16mA 3.3/0.016 = 206 Let's go higher and say 220R
D1 is any rectifier diode capable of carrying a continuous current of 2 Amps or more.
Front Circuits
POWER
Diagonal Circuits
RIGHT MOTOR
BATTERY
Serpent Scamper Chassis Board Schematic
LEFT MOTOR
Battery Monitor

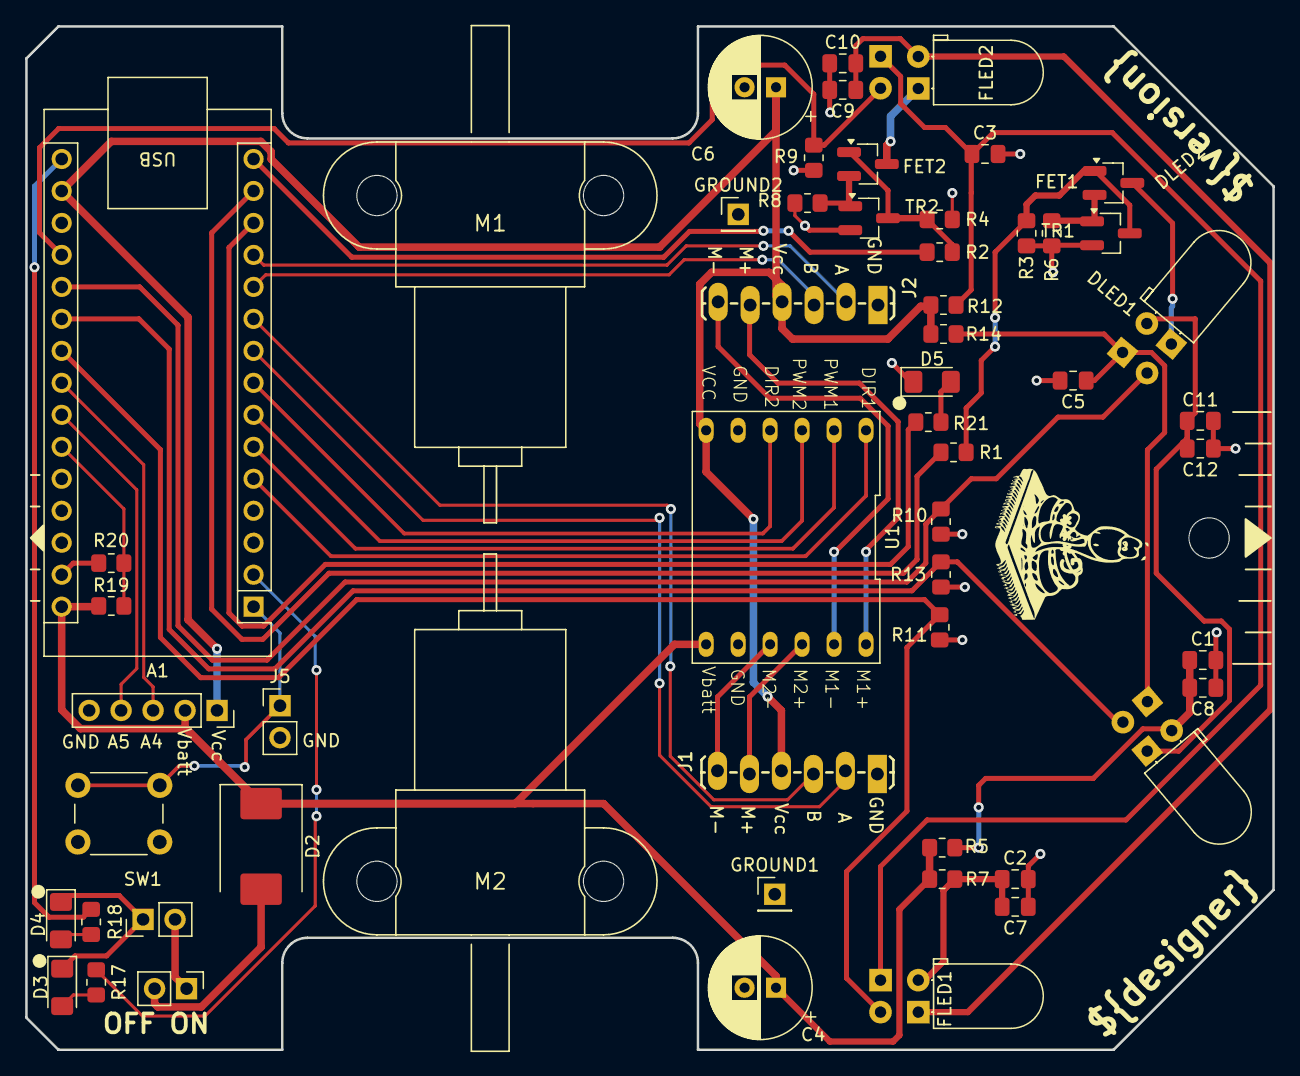
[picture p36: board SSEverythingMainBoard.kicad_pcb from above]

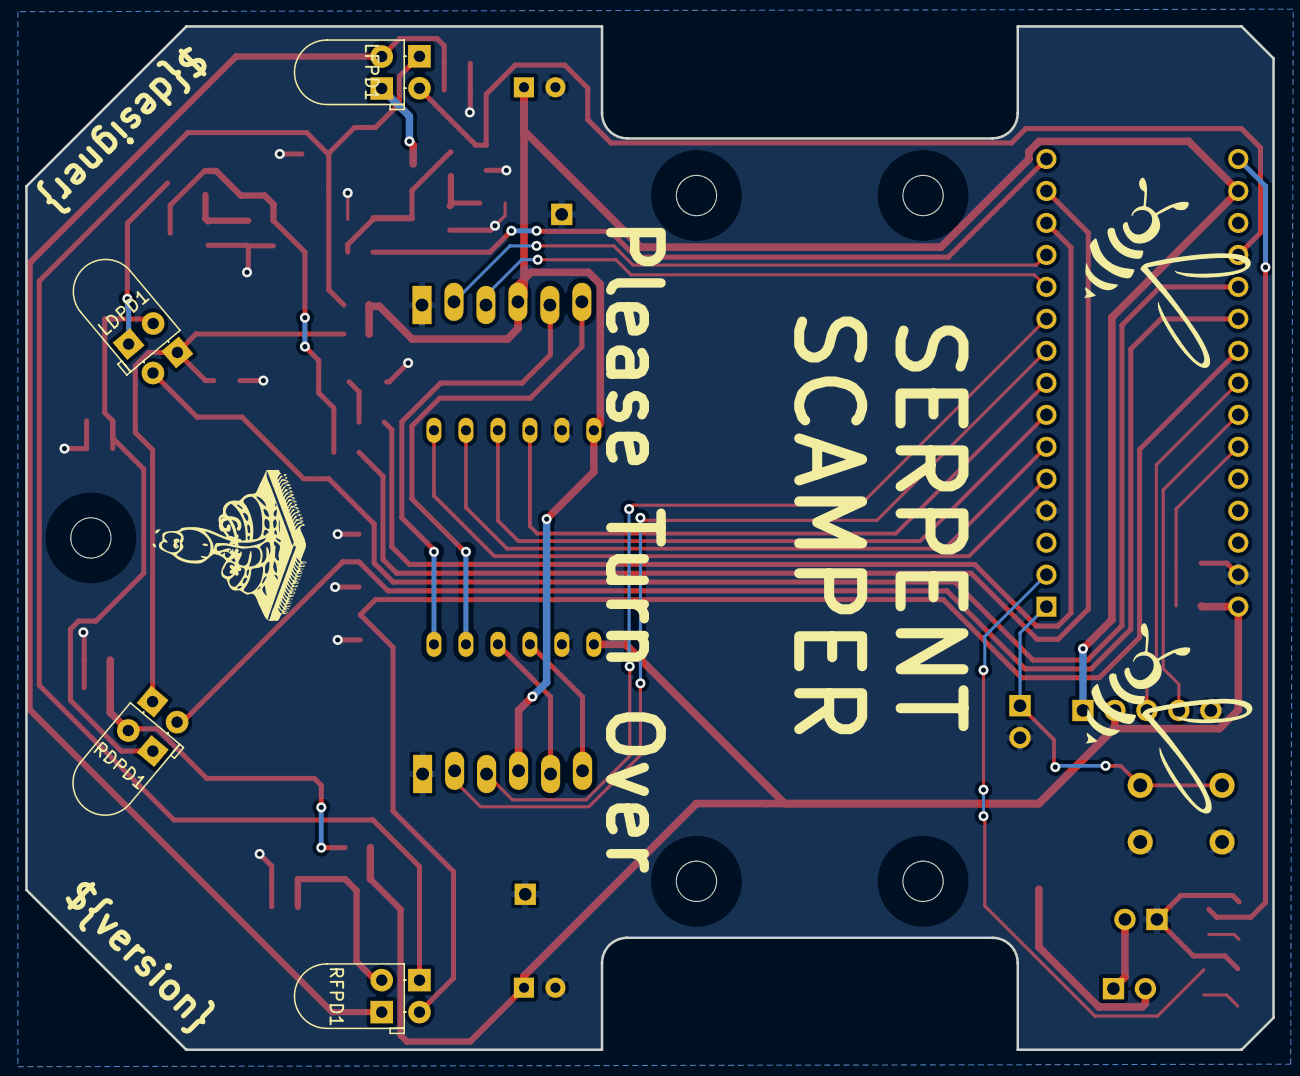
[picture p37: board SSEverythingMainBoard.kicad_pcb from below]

Board: 2 copper layers, 99.1 x 81.3 mm, 64 parts (4 on the bottom side), 45 nets.

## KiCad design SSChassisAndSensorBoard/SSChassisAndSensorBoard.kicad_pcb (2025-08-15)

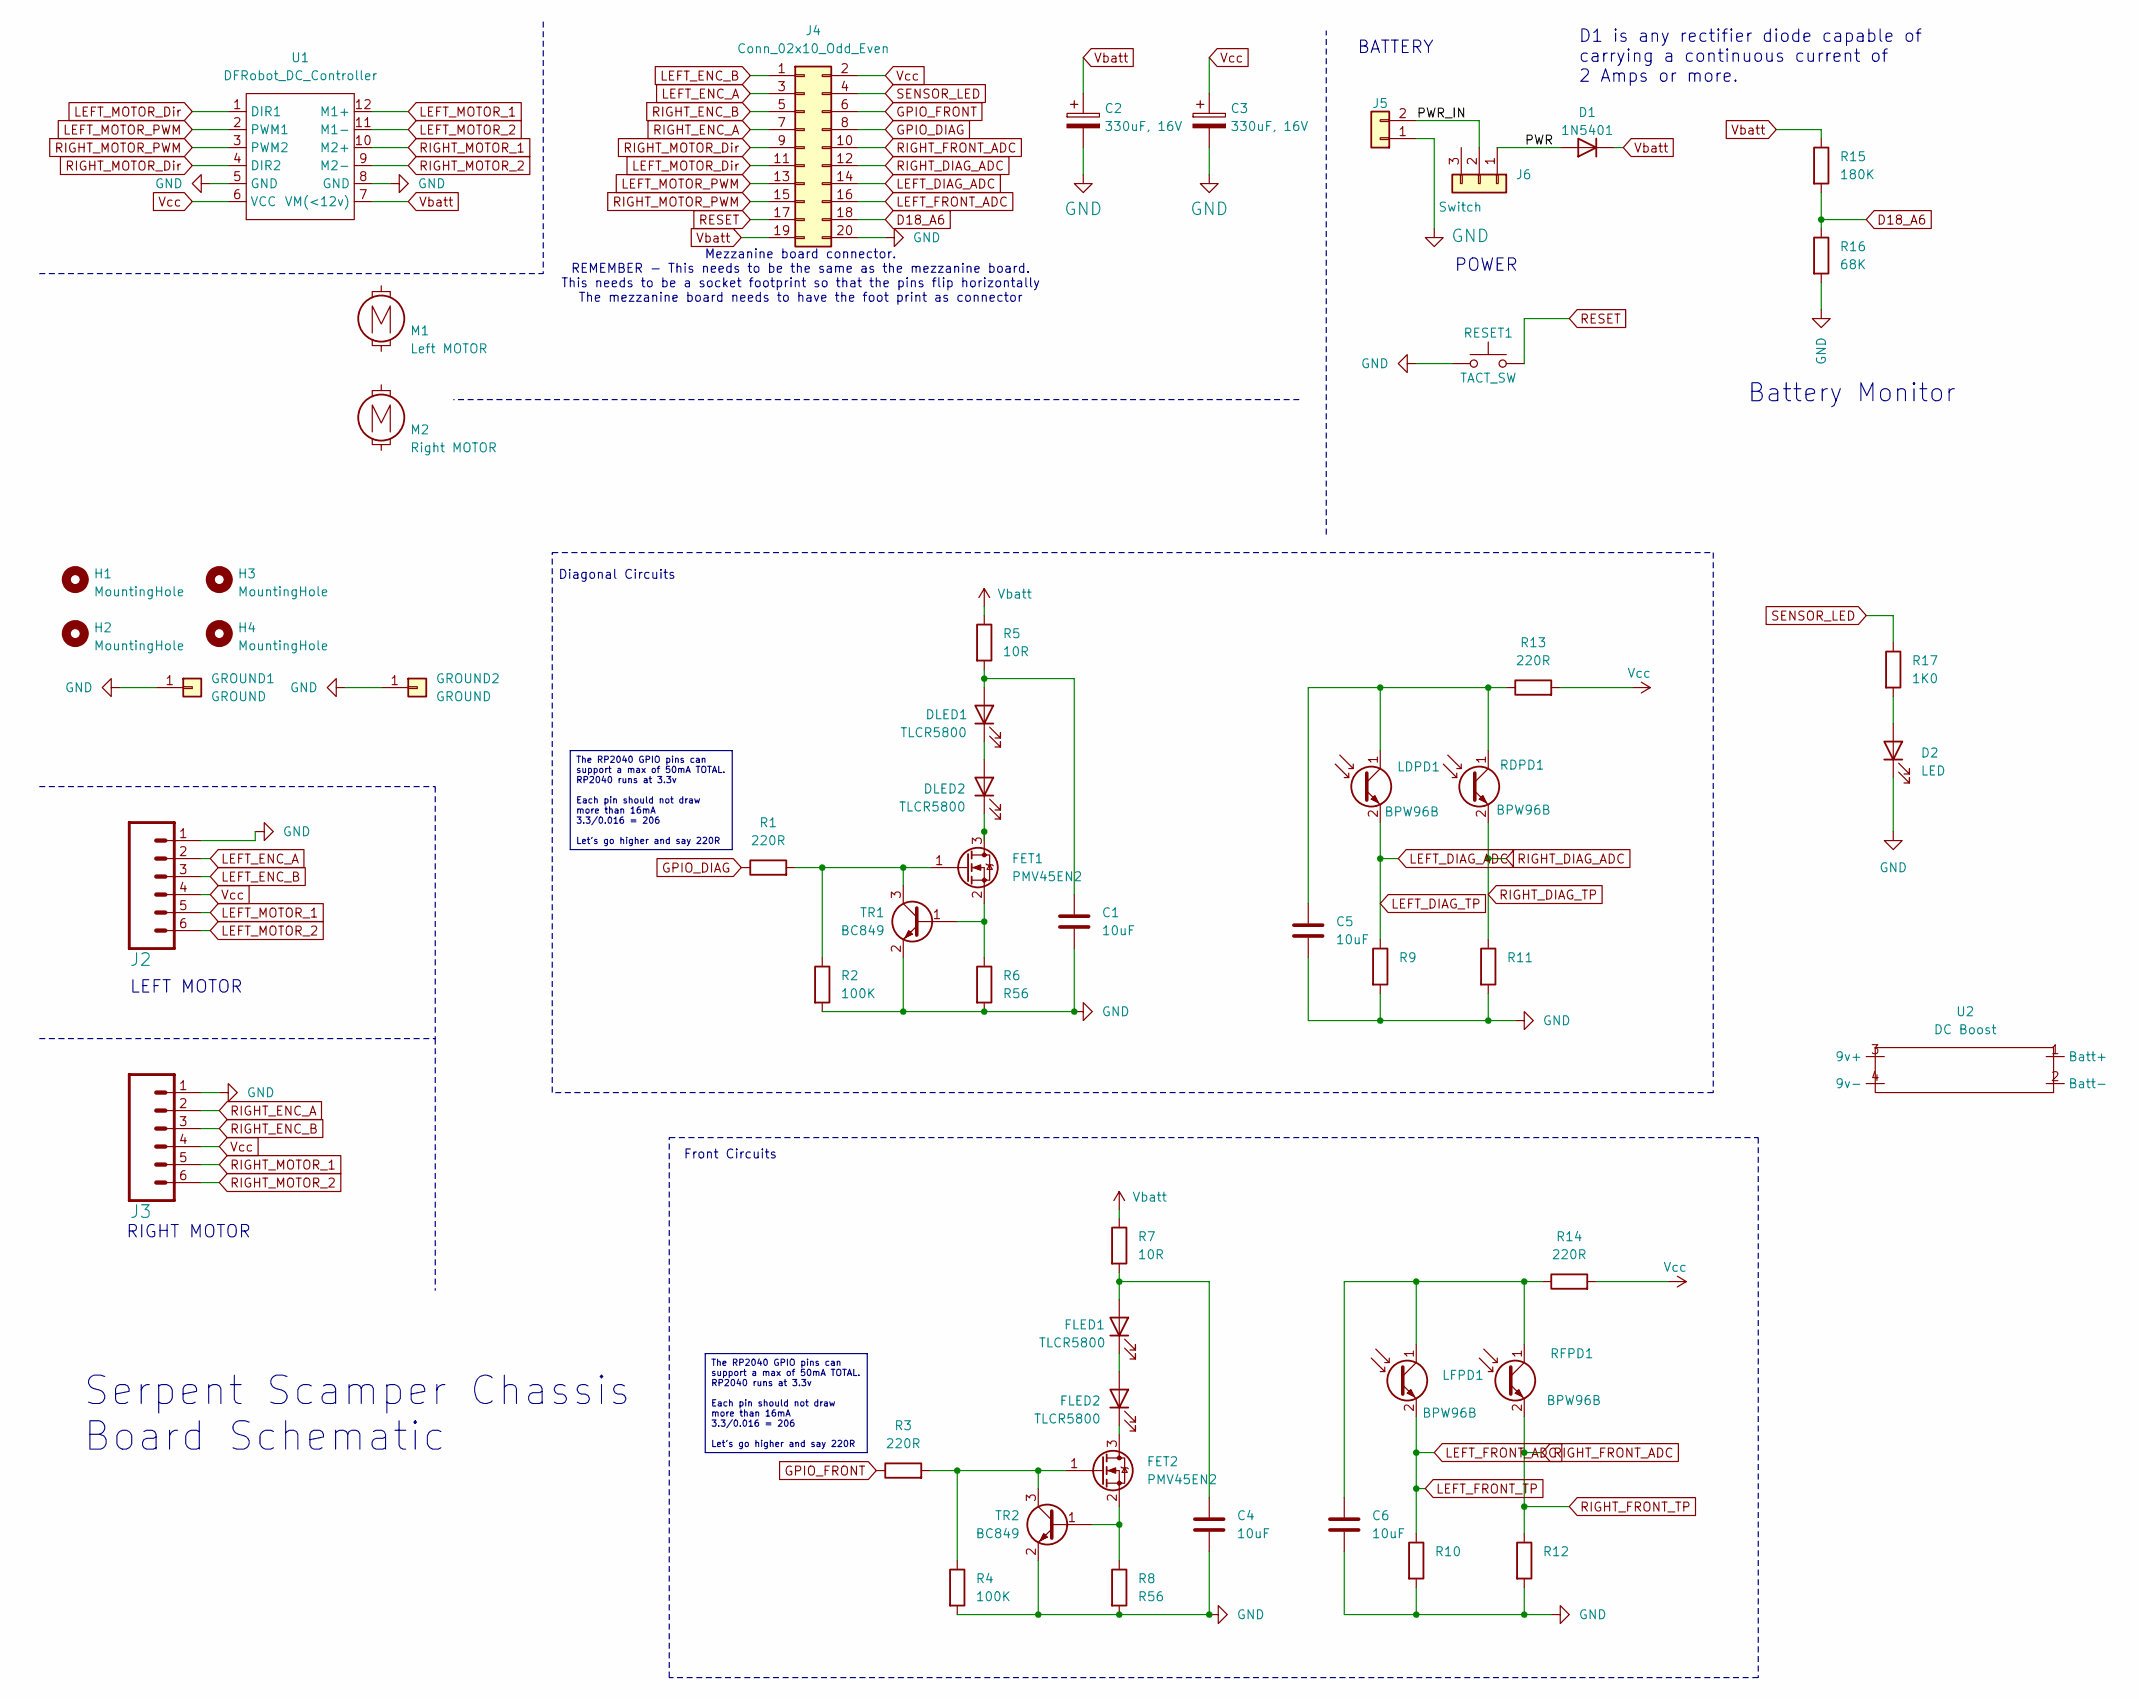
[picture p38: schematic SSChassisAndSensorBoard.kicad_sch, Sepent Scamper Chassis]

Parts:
C1, C4, C5, C6: 10uF; C_0805_2012Metric_Pad1.18x1.45mm_HandSolder
C2, C3: 330uF, 16V; CP_Radial_D8.0mm_P2.50mm
D1: 1N5401; D_DO-201AD_P15.24mm_Horizontal
D2: LED; LED_1206_3216Metric_Pad1.42x1.75mm_HandSolder
DLED1, DLED2: TLCR5800; LED_D5.0mm_Horizontal_O1.27mm_Z3.0mm
FET1, FET2: PMV45EN2; SOT-23_Handsoldering
FLED1, FLED2: TLCR5800; LED_D5.0mm_Horizontal_O1.27mm_Z3.0mm
GROUND1, GROUND2: GROUND; PinHeader_1x01_P2.54mm_Vertical
H1, H2, H3, H4: MountingHole; MountingHole_3.2mm_M3_clearance
J2, J3: CONN_06SILK_FEMALE_PTH; 1X06_LOCK_LONGPADS
J4: Conn_02x10_Odd_Even; PinSocket_2x10_P2.54mm_Vertical
J5: POWER; Molex_KK-254_AE-6410-02A_1x02_P2.54mm_Vertical
J6: Switch; PinHeader_1x03_P2.54mm_Vertical
LDPD1: BPW96B; LED_D5.0mm_Horizontal_O1.27mm_Z3.0mm
LFPD1: BPW96B; LED_D5.0mm_Horizontal_O1.27mm_Z3.0mm
M1: Left MOTOR; MINI-METAL-GEARMOTOR-WITH-BRACKET_Alt
M2: Right MOTOR; MINI-METAL-GEARMOTOR-WITH-BRACKET
R1, R3, R13, R14: 220R; R_0805_2012Metric_Pad1.20x1.40mm_HandSolder
R2, R4: 100K; R_0805_2012Metric_Pad1.20x1.40mm_HandSolder
R5, R7: 10R; R_0805_2012Metric_Pad1.20x1.40mm_HandSolder
R6, R8: R56; R_0805_2012Metric_Pad1.20x1.40mm_HandSolder
R9, R10, R11, R12: R; R_0805_2012Metric_Pad1.20x1.40mm_HandSolder
R15: 180K; R_Axial_DIN0207_L6.3mm_D2.5mm_P7.62mm_Horizontal
R16: 68K; R_Axial_DIN0207_L6.3mm_D2.5mm_P7.62mm_Horizontal
R17: 1K0; R_0805_2012Metric_Pad1.20x1.40mm_HandSolder
RDPD1: BPW96B; LED_D5.0mm_Horizontal_O1.27mm_Z3.0mm
RESET1: TACT_SW; SW_PUSH_6mm
RFPD1: BPW96B; LED_D5.0mm_Horizontal_O1.27mm_Z3.0mm
TR1, TR2: BC849; SOT-23_Handsoldering
U1: DFRobot_DC_Controller
U2: DC Boost

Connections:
/PWR: D1.2 (A), J6.1
/PWR_IN: J5.2, J6.2
D18_A6: J4.18, R15.2, R16.1
GND: C1.2, C2.2, C3.2, C4.2, C5.2, C6.2, D2.1 (K), GROUND1.1, GROUND2.1, J2.1, J3.1, J4.20, J5.1, R2.2, R4.2, R6.2, R8.2, R9.2, R10.2, R11.2, R12.2, R16.2, RESET1.1 (A), TR1.2 (E), TR2.2 (E), U1.5 (GND), U1.8 (GND)
GPIO_DIAG: J4.8, R1.1
GPIO_FRONT: J4.6, R3.1
LEFT_DIAG_ADC: J4.14, LDPD1.2 (E), R9.1
LEFT_ENC_A: J2.2, J4.3
LEFT_ENC_B: J2.3, J4.1
LEFT_FRONT_ADC: J4.16, LFPD1.2 (E), R10.1
LEFT_MOTOR_1: J2.5, U1.12 (M1+)
LEFT_MOTOR_2: J2.6, U1.11 (M1-)
LEFT_MOTOR_Dir: J4.11, U1.1 (DIR1)
LEFT_MOTOR_PWM: J4.13, U1.2 (PWM1)
unnamed: D2.2 (A), R17.2
unnamed: C1.1, DLED1.2 (A), R5.2
unnamed: DLED1.1 (K), DLED2.2 (A)
unnamed: DLED2.1 (K), FET1.3 (D)
unnamed: FET1.1 (G), R1.2, R2.1, TR1.3 (C)
unnamed: FET1.2 (S), R6.1, TR1.1 (B)
unnamed: FET2.3 (D), FLED2.1 (K)
unnamed: FET2.1 (G), R3.2, R4.1, TR2.3 (C)
unnamed: FET2.2 (S), R8.1, TR2.1 (B)
unnamed: C4.1, FLED1.2 (A), R7.2
unnamed: FLED1.1 (K), FLED2.2 (A)
unnamed: C5.1, LDPD1.1 (C), R13.1, RDPD1.1 (C)
unnamed: C6.1, LFPD1.1 (C), R14.1, RFPD1.1 (C)
RESET: J4.17, RESET1.2 (B)
RIGHT_DIAG_ADC: J4.12, R11.1, RDPD1.2 (E)
RIGHT_ENC_A: J3.2, J4.7
RIGHT_ENC_B: J3.3, J4.5
RIGHT_FRONT_ADC: J4.10, R12.1, RFPD1.2 (E)
RIGHT_MOTOR_1: J3.5, U1.10 (M2+)
RIGHT_MOTOR_2: J3.6, U1.9 (M2-)
RIGHT_MOTOR_Dir: J4.9, U1.4 (DIR2)
RIGHT_MOTOR_PWM: J4.15, U1.3 (PWM2)
SENSOR_LED: J4.4, R17.1
Vbatt: C2.1, D1.1 (K), J4.19, R5.1, R7.1, R15.1, U1.7 (VM(<12v))
Vcc: C3.1, J2.4, J3.4, J4.2, R13.2, R14.2, U1.6 (VCC)

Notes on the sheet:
The RP2040 GPIO pins can support a max of 50mA TOTAL. RP2040 runs at 3.3v Each pin should not draw more than 16mA 3.3/0.016 = 206 Let's go higher and say 220R
D1 is any rectifier diode capable of carrying a continuous current of 2 Amps or more.
Front Circuits
POWER
Diagonal Circuits
RIGHT MOTOR
BATTERY
Mezzanine board connector. REMEMBER - This needs to be the same as the mezzanine board. This needs to be a socket footprint so that the pins flip horizontally The mezzanine board needs to have the foot print as connector
Serpent Scamper Chassis Board Schematic
LEFT MOTOR
Battery Monitor

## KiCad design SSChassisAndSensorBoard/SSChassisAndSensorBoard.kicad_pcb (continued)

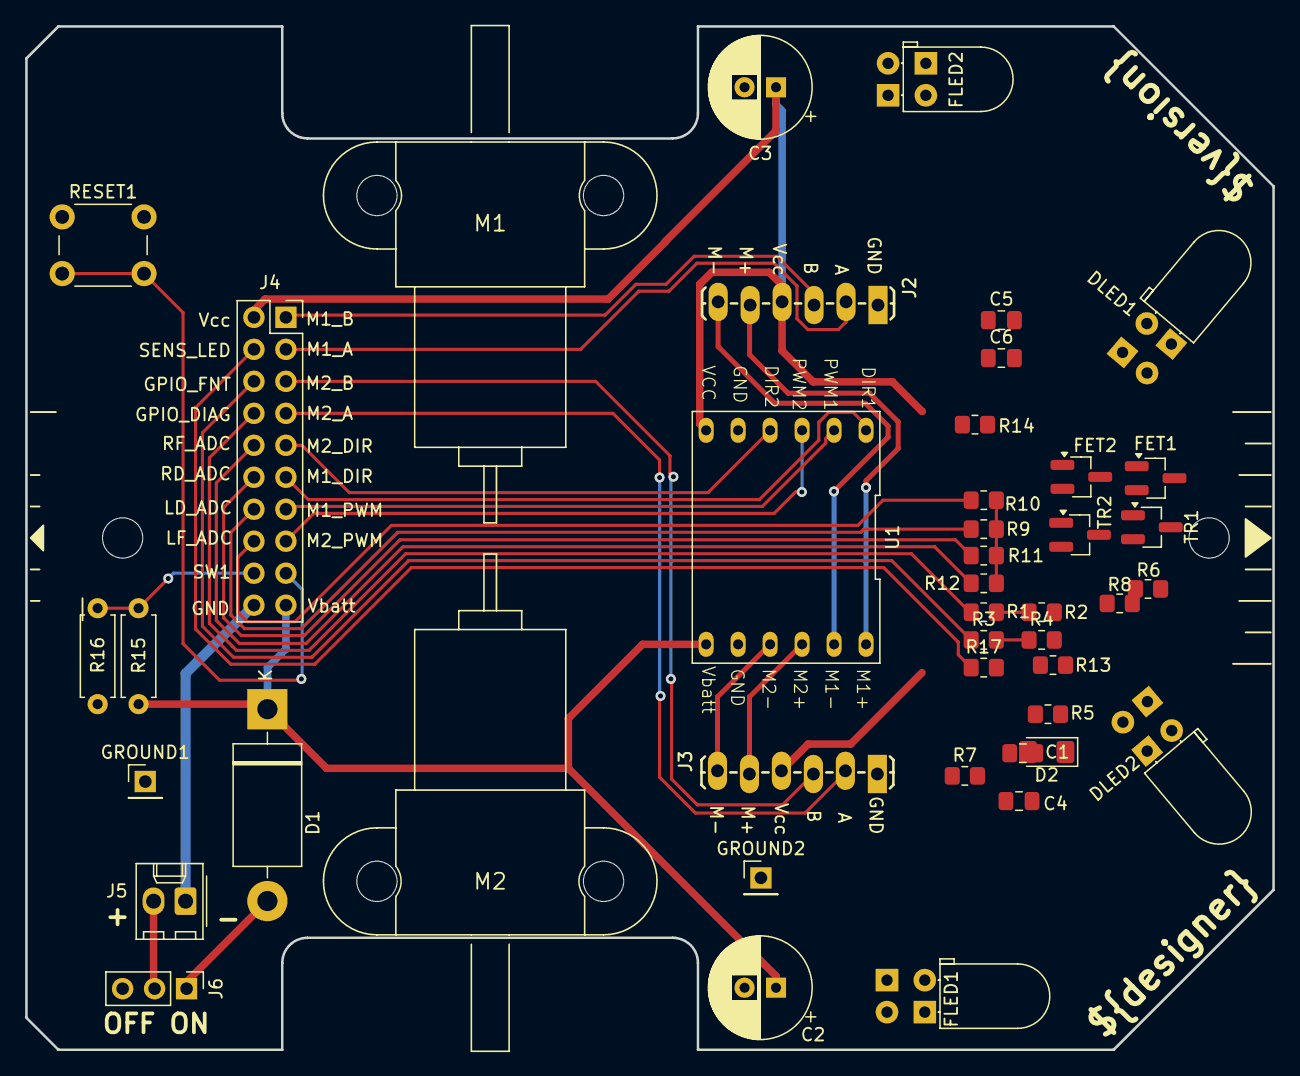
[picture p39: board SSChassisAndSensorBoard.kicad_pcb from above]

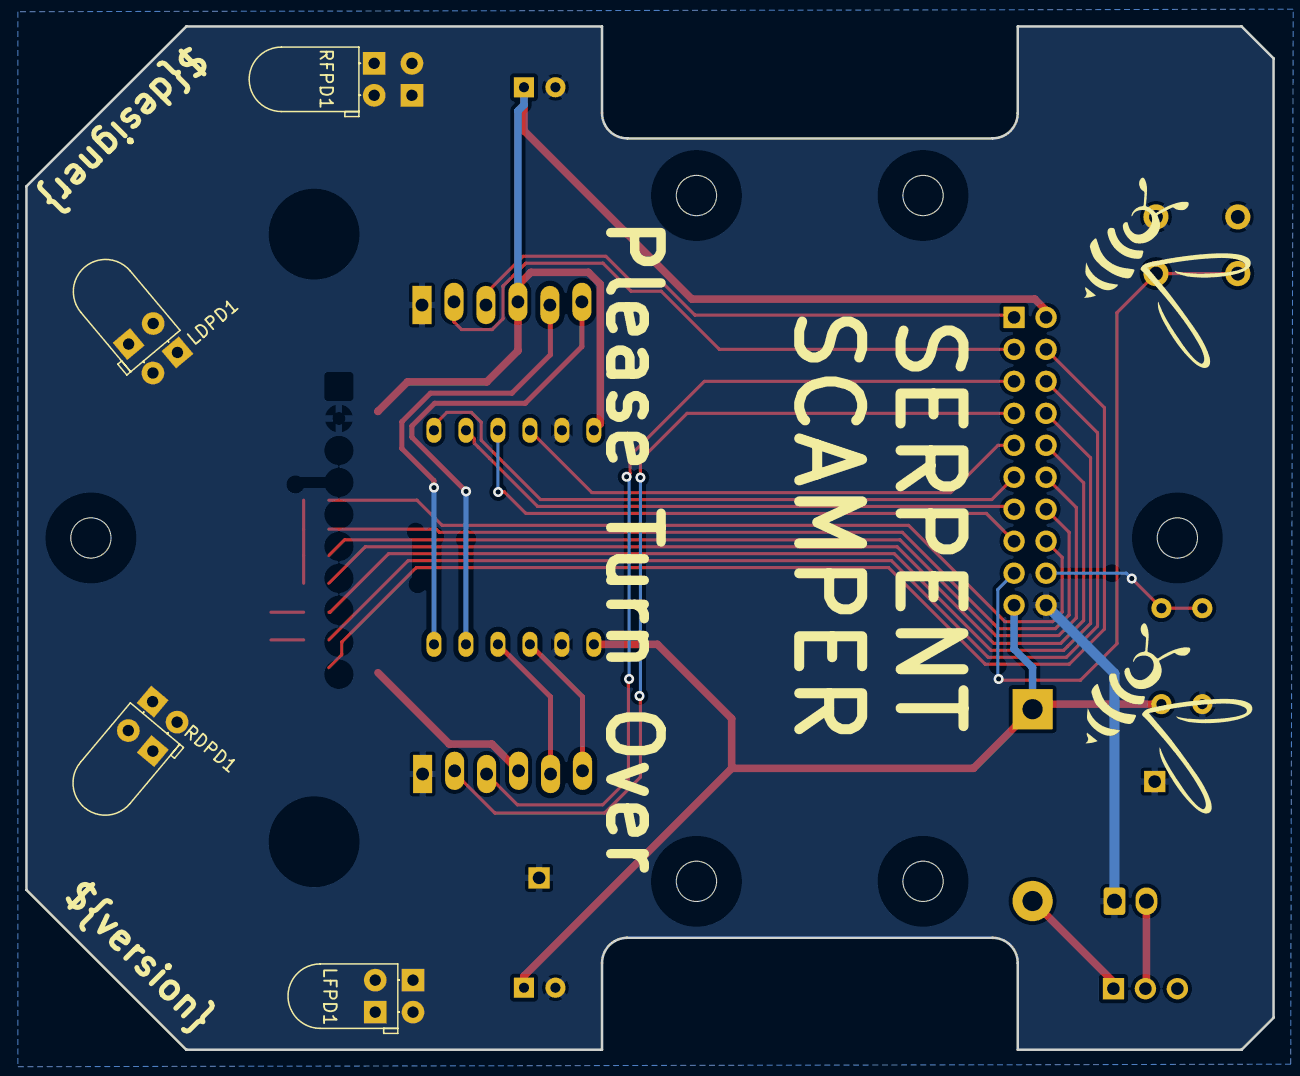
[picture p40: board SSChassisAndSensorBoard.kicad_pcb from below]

Board: 2 copper layers, 99.1 x 81.3 mm, 52 parts (4 on the bottom side), 39 nets.

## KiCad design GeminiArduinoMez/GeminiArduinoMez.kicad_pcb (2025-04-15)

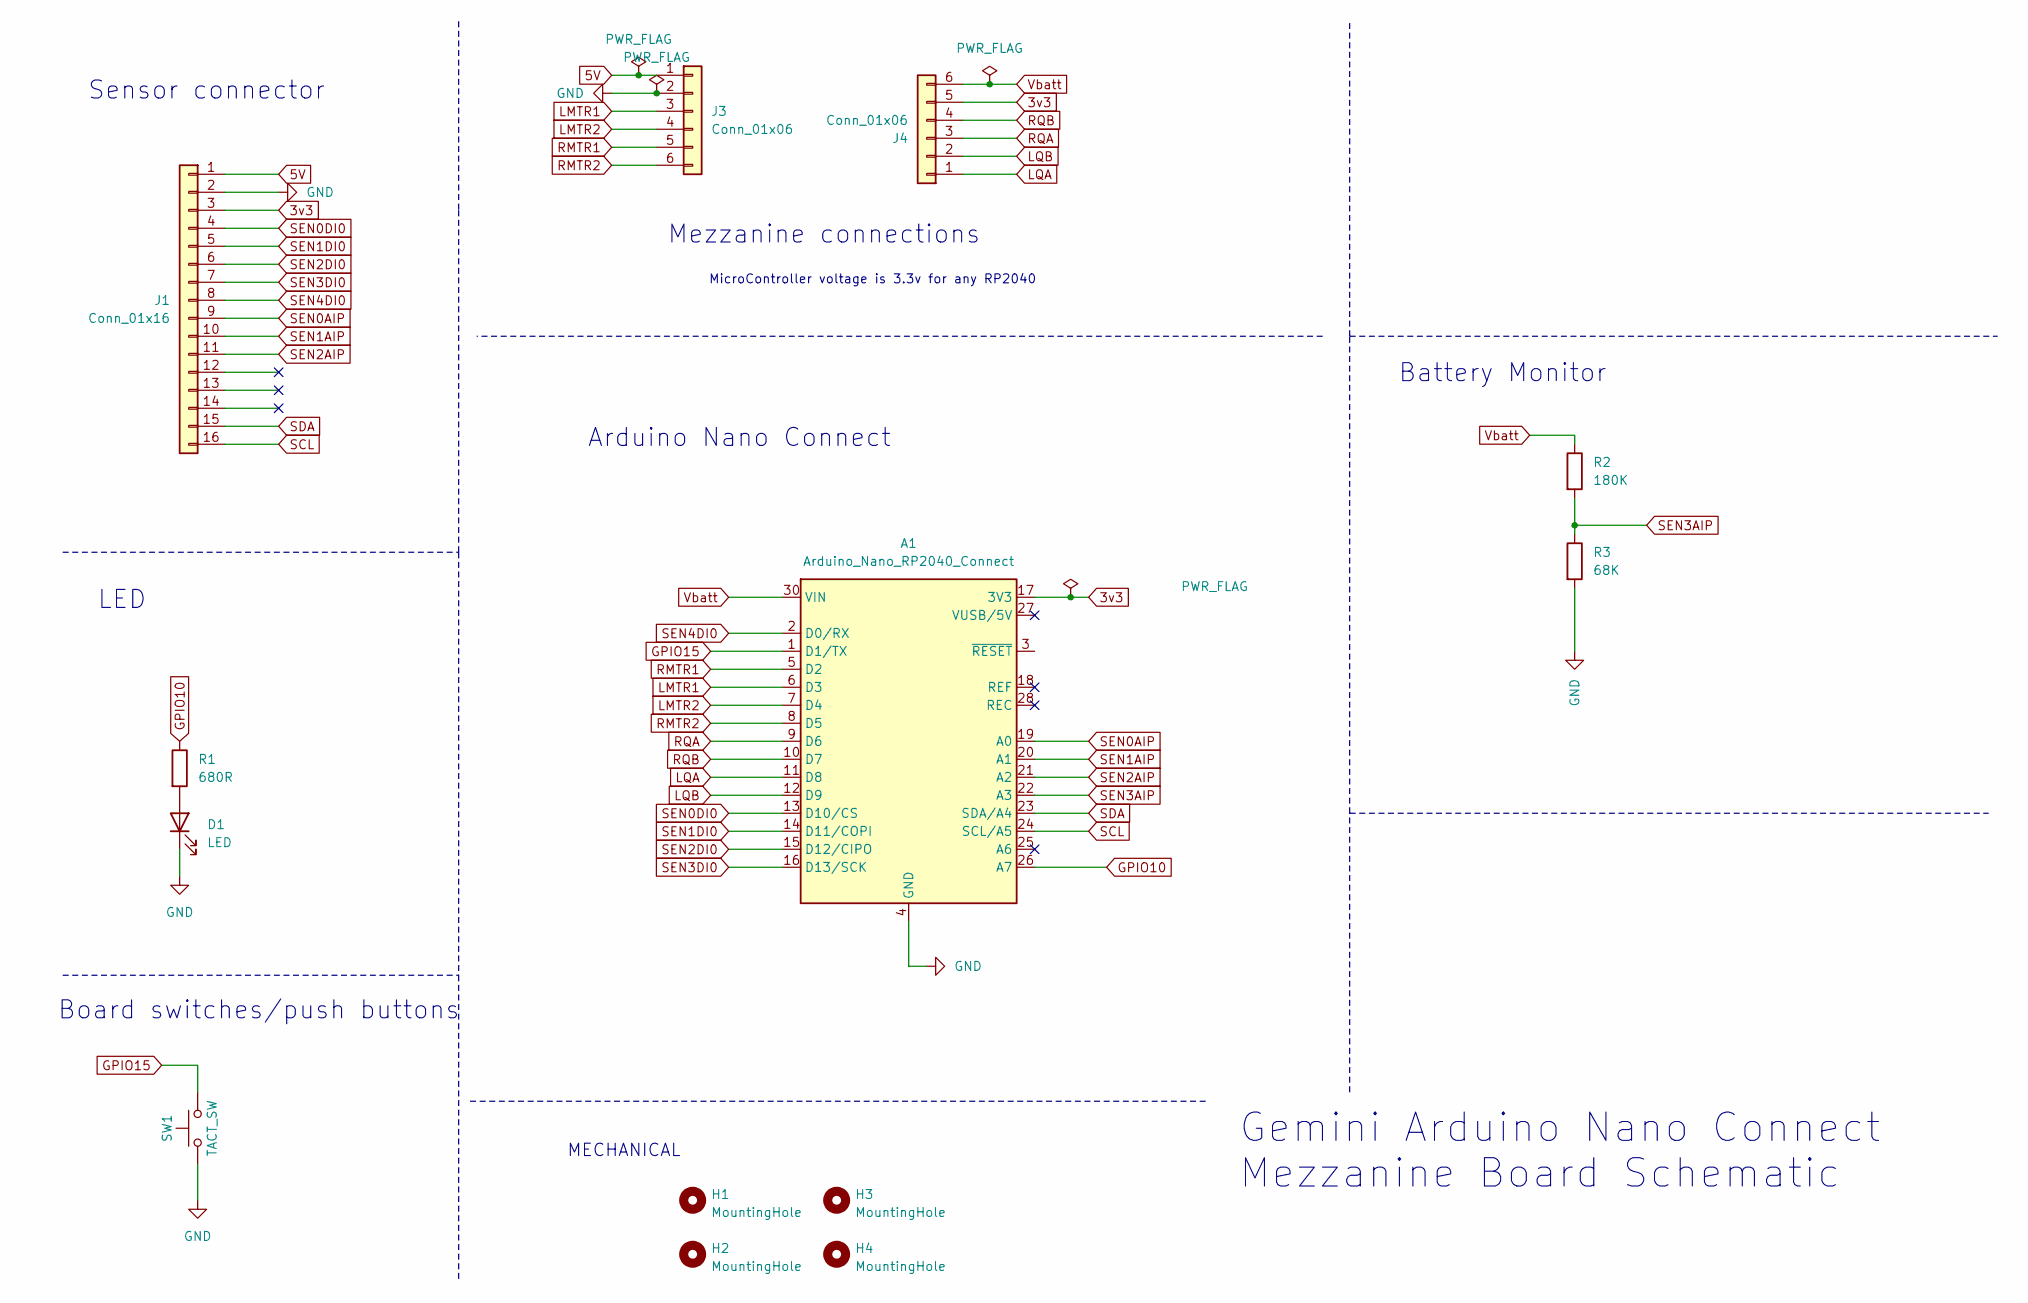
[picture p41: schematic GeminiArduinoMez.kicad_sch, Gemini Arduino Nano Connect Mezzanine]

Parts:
A1: Arduino_Nano_RP2040_Connect; Arduino_Nano
D1: LED; LED_D5.0mm
H1, H2, H3, H4: MountingHole; MountingHole_3.2mm_M3_clearance
J1: Conn_01x16; PinHeader_1x16_P2.54mm_Vertical
J3, J4: Conn_01x06; PinHeader_1x06_P2.54mm_Vertical
R1: 680R; R_Axial_DIN0207_L6.3mm_D2.5mm_P7.62mm_Horizontal
R2: 180K; R_Axial_DIN0207_L6.3mm_D2.5mm_P7.62mm_Horizontal
R3: 68K; R_Axial_DIN0207_L6.3mm_D2.5mm_P7.62mm_Horizontal
SW1: TACT_SW; SW_PUSH_6mm

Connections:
3v3: A1.17 (3V3), J1.3, J4.5
5V: J1.1, J3.1
GND: A1.4 (GND), A1.29 (GND), D1.1 (K), J1.2, J3.2, R3.2, SW1.1 (A)
GPIO10: A1.26 (A7), R1.1
GPIO15: A1.1 (D1/TX), SW1.2 (B)
LMTR1: A1.6 (D3), J3.3
LMTR2: A1.7 (D4), J3.4
LQA: A1.11 (D8), J4.1
LQB: A1.12 (D9), J4.2
unnamed: D1.2 (A), R1.2
RMTR1: A1.5 (D2), J3.5
RMTR2: A1.8 (D5), J3.6
RQA: A1.9 (D6), J4.3
RQB: A1.10 (D7), J4.4
SCL: A1.24 (SCL/A5), J1.16
SDA: A1.23 (SDA/A4), J1.15
SEN0AIP: A1.19 (A0), J1.9
SEN0DI0: A1.13 (D10/CS), J1.4
SEN1AIP: A1.20 (A1), J1.10
SEN1DI0: A1.14 (D11/COPI), J1.5
SEN2AIP: A1.21 (A2), J1.11
SEN2DI0: A1.15 (D12/CIPO), J1.6
SEN3AIP: A1.22 (A3), R2.2, R3.1
SEN3DI0: A1.16 (D13/SCK), J1.7
SEN4DI0: A1.2 (D0/RX), J1.8
Vbatt: A1.30 (VIN), J4.6, R2.1

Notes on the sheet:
Board switches/push buttons
MicroController voltage is 3.3v for any RP2040
LED
Sensor connector
MECHANICAL
Arduino Nano Connect
Mezzanine connections
Gemini Arduino Nano Connect Mezzanine Board Schematic
Battery Monitor

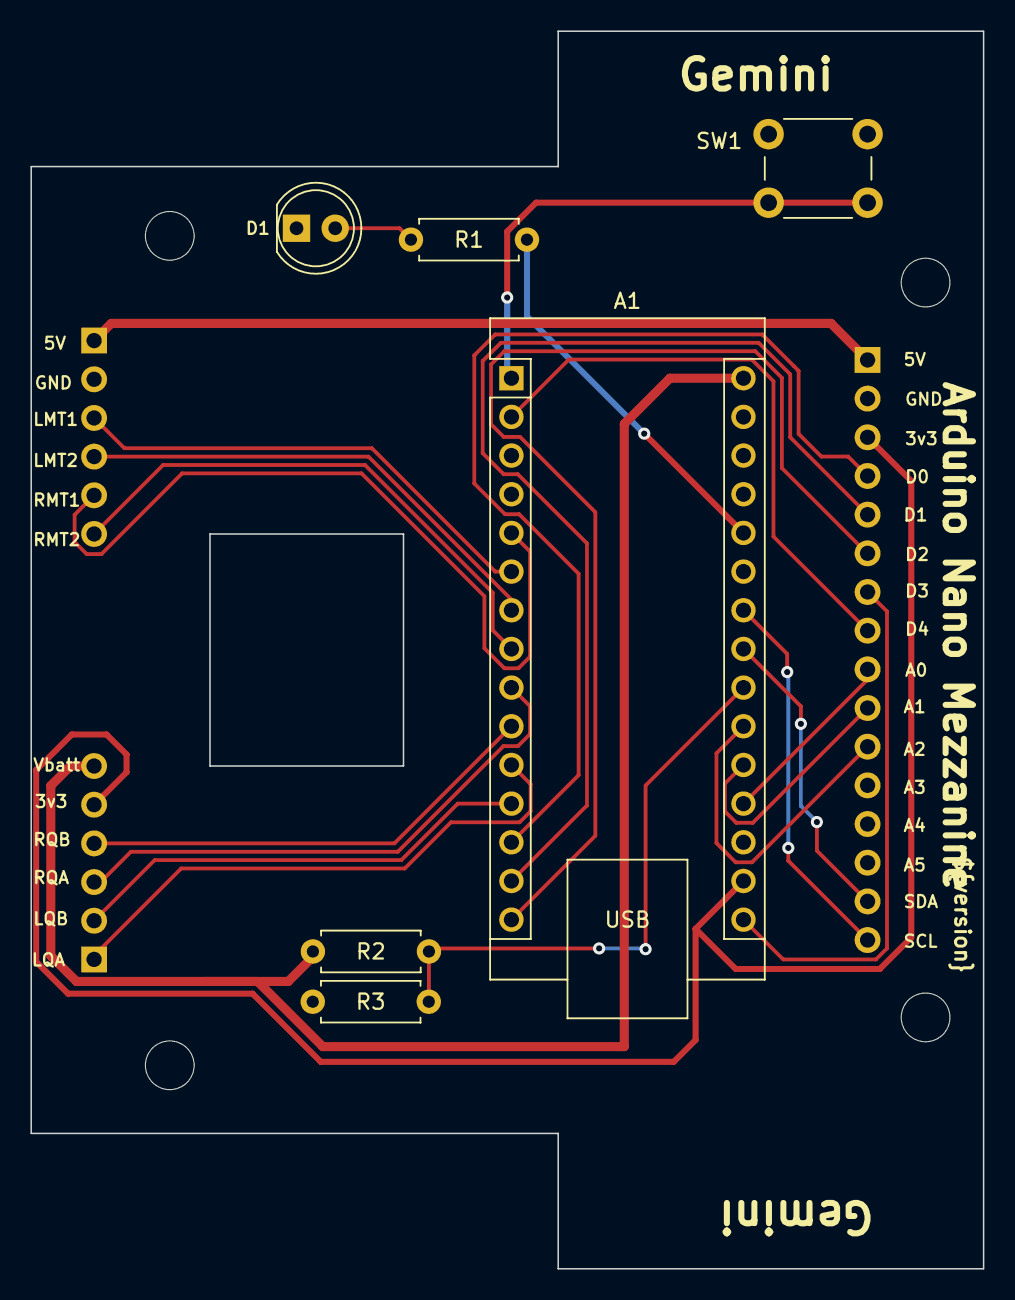
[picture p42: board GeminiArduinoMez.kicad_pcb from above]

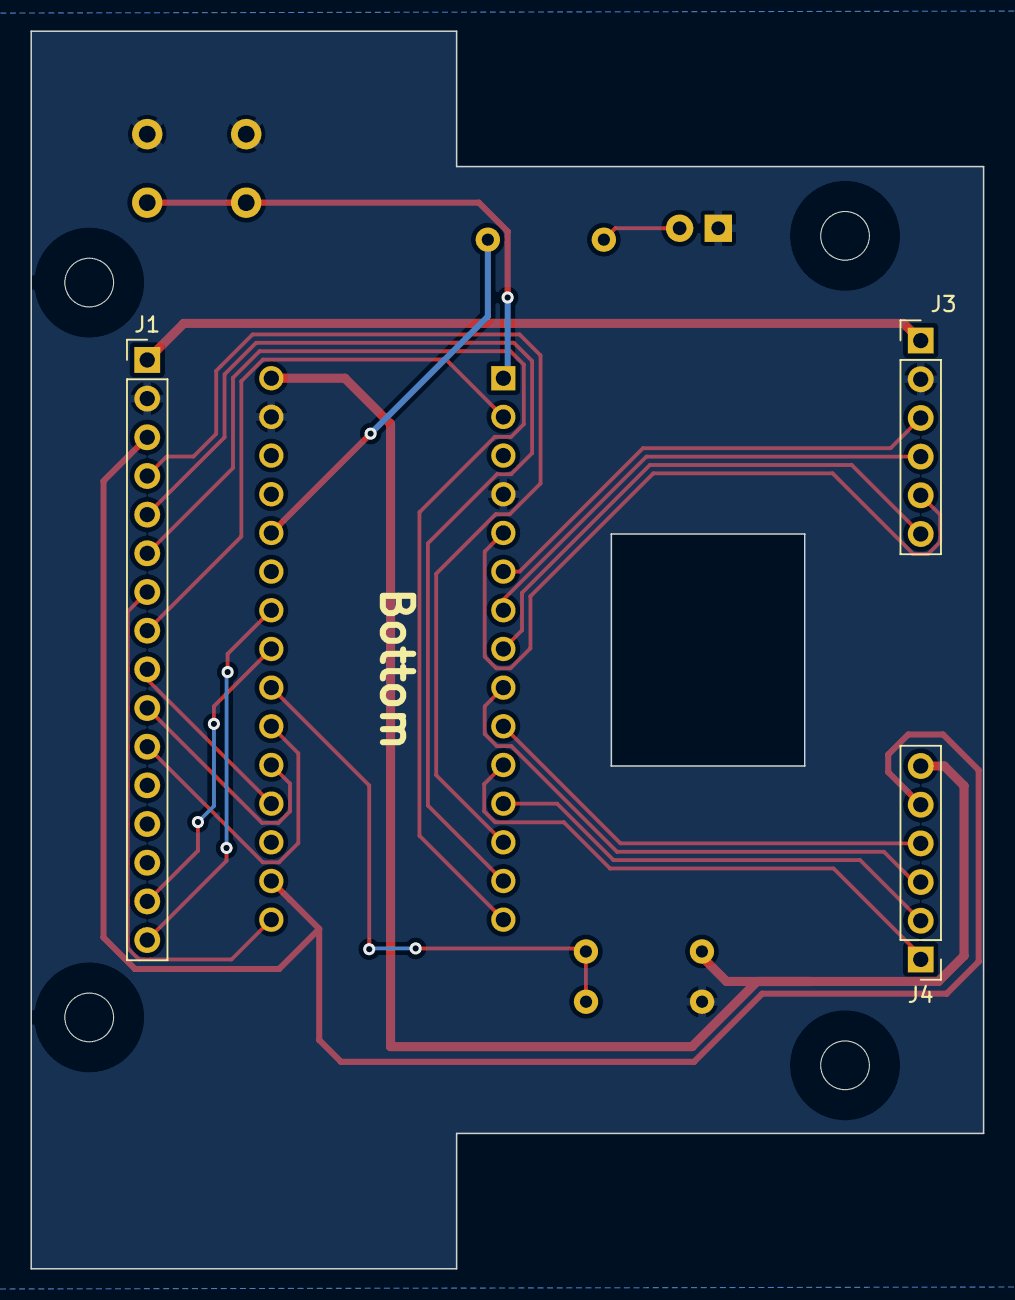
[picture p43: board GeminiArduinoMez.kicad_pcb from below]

Board: 2 copper layers, 62.5 x 81.3 mm, 13 parts (3 on the bottom side), 26 nets.

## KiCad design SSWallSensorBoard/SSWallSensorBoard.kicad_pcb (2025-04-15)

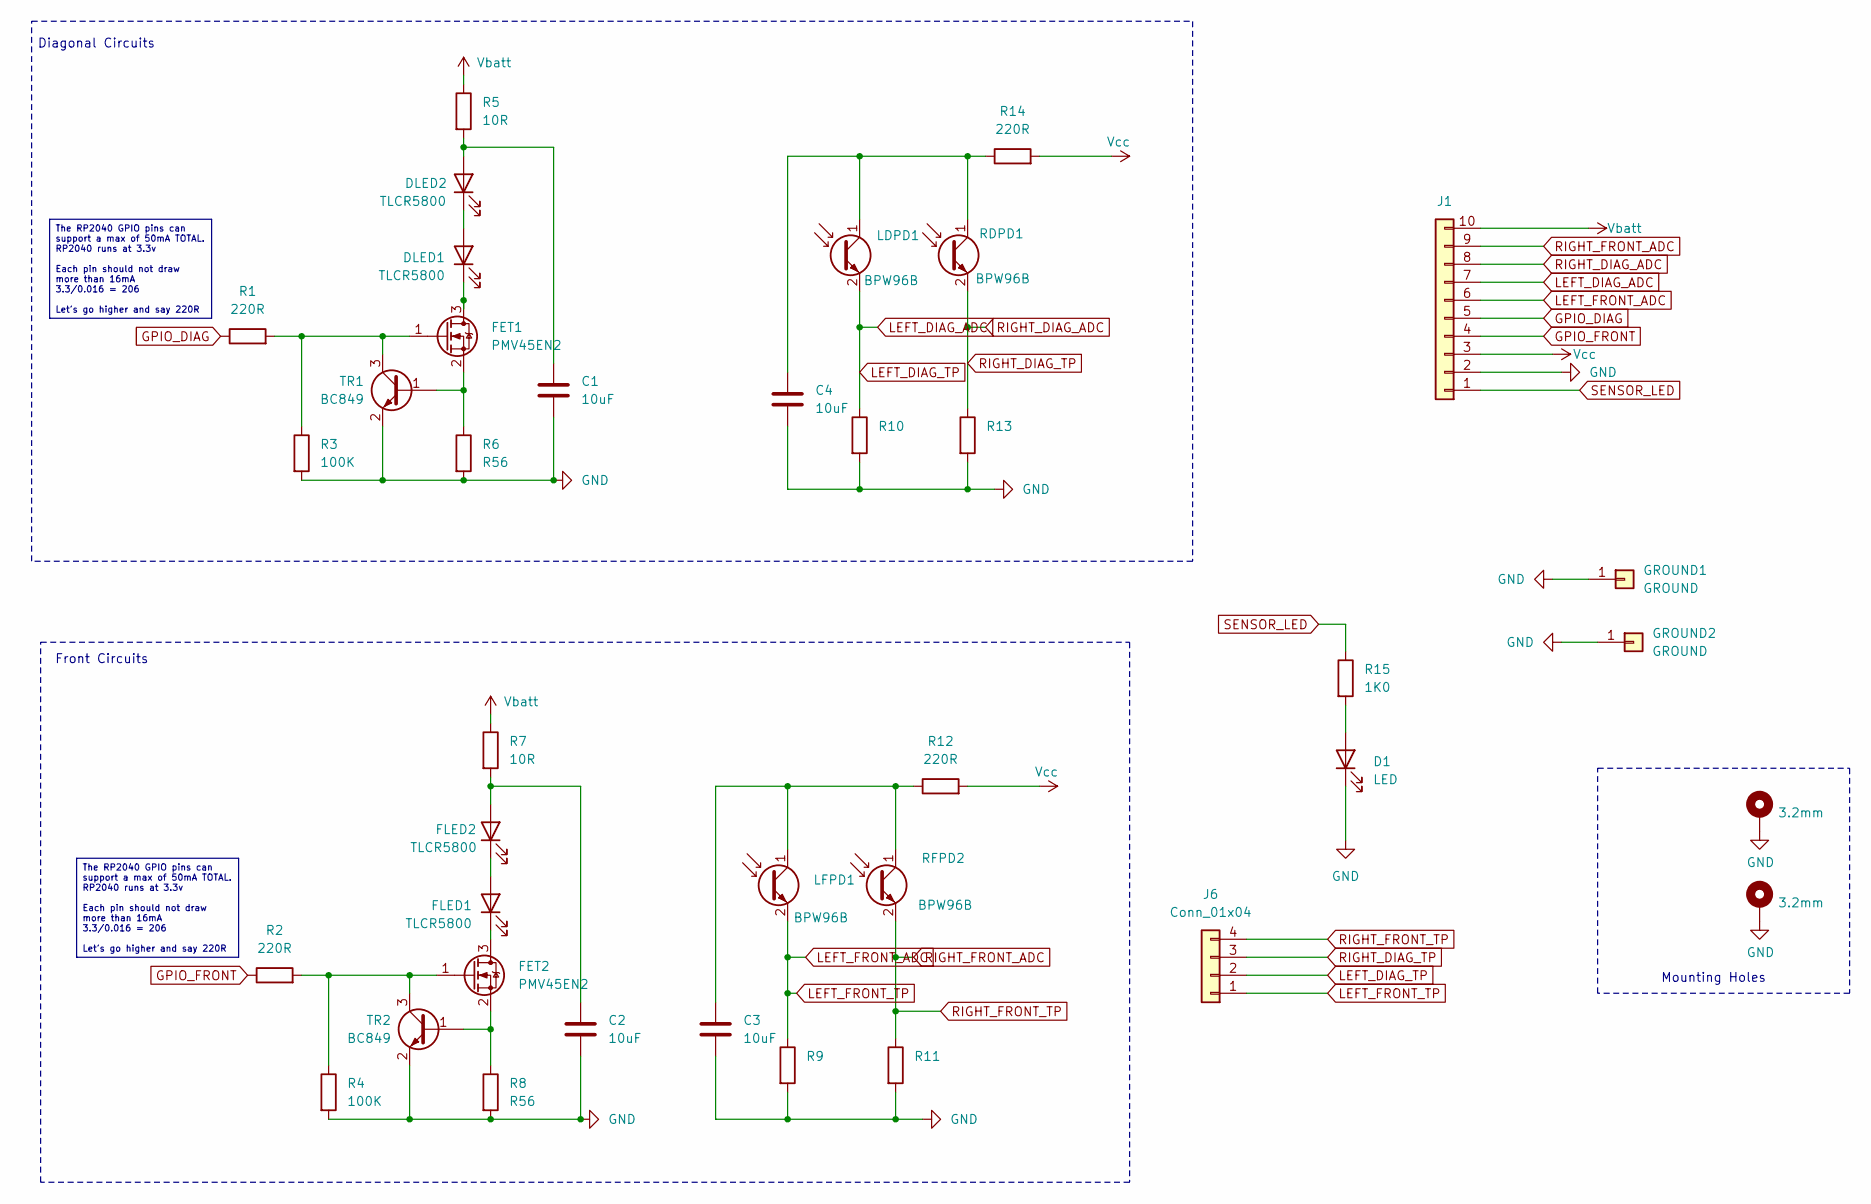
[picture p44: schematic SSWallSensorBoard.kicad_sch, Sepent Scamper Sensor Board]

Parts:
C1, C2, C3, C4: 10uF; C_0805_2012Metric_Pad1.18x1.45mm_HandSolder
D1: LED; LED_1206_3216Metric_Pad1.42x1.75mm_HandSolder
DLED1, DLED2: TLCR5800; LED_D5.0mm_Horizontal_O1.27mm_Z3.0mm
FET1, FET2: PMV45EN2; SOT-23_Handsoldering
FLED1, FLED2: TLCR5800; LED_D5.0mm_Horizontal_O1.27mm_Z3.0mm
GROUND1, GROUND2: GROUND; PinHeader_1x01_P2.54mm_Vertical
H1, H2: 3.2mm; MountingHole_3.2mm_M3_Pad
J1: Conn_01x10; PinHeader_1x10_P2.54mm_Vertical
J6: Conn_01x04; PinHeader_1x04_P2.54mm_Vertical
LDPD1: BPW96B; LED_D5.0mm_Horizontal_O1.27mm_Z3.0mm
LFPD1: BPW96B; LED_D5.0mm_Horizontal_O1.27mm_Z3.0mm
R1, R2, R12, R14: 220R; R_0805_2012Metric_Pad1.20x1.40mm_HandSolder
R3, R4: 100K; R_0805_2012Metric_Pad1.20x1.40mm_HandSolder
R5, R7: 10R; R_0805_2012Metric_Pad1.20x1.40mm_HandSolder
R6, R8: R56; R_0805_2012Metric_Pad1.20x1.40mm_HandSolder
R9, R10, R11, R13: R; R_0805_2012Metric_Pad1.20x1.40mm_HandSolder
R15: 1K0; R_0805_2012Metric_Pad1.20x1.40mm_HandSolder
RDPD1: BPW96B; LED_D5.0mm_Horizontal_O1.27mm_Z3.0mm
RFPD2: BPW96B; LED_D5.0mm_Horizontal_O1.27mm_Z3.0mm
TR1, TR2: BC849; SOT-23_Handsoldering

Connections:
GND: C1.2, C2.2, C3.2, C4.2, D1.1 (K), GROUND1.1, GROUND2.1, H1.1, H2.1, J1.2, R3.2, R4.2, R6.2, R8.2, R9.2, R10.2, R11.2, R13.2, TR1.2 (E), TR2.2 (E)
GPIO_DIAG: J1.5, R1.1
GPIO_FRONT: J1.4, R2.1
LEFT_DIAG_ADC: J1.7, J6.2, LDPD1.2 (E), R10.1
LEFT_FRONT_ADC: J1.6, J6.1, LFPD1.2 (E), R9.1
unnamed: D1.2 (A), R15.2
unnamed: DLED1.2 (A), DLED2.1 (K)
unnamed: DLED1.1 (K), FET1.3 (D)
unnamed: C1.1, DLED2.2 (A), R5.2
unnamed: FET1.1 (G), R1.2, R3.1, TR1.3 (C)
unnamed: FET1.2 (S), R6.1, TR1.1 (B)
unnamed: FET2.3 (D), FLED1.1 (K)
unnamed: FET2.1 (G), R2.2, R4.1, TR2.3 (C)
unnamed: FET2.2 (S), R8.1, TR2.1 (B)
unnamed: FLED1.2 (A), FLED2.1 (K)
unnamed: C2.1, FLED2.2 (A), R7.2
unnamed: C4.1, LDPD1.1 (C), R14.1, RDPD1.1 (C)
unnamed: C3.1, LFPD1.1 (C), R12.1, RFPD2.1 (C)
RIGHT_DIAG_ADC: J1.8, J6.3, R13.1, RDPD1.2 (E)
RIGHT_FRONT_ADC: J1.9, J6.4, R11.1, RFPD2.2 (E)
SENSOR_LED: J1.1, R15.1
Vbatt: J1.10, R5.1, R7.1
Vcc: J1.3, R12.2, R14.2

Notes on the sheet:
The RP2040 GPIO pins can support a max of 50mA TOTAL. RP2040 runs at 3.3v Each pin should not draw more than 16mA 3.3/0.016 = 206 Let's go higher and say 220R
Diagonal Circuits
Mounting Holes
Front Circuits



Board: 2 copper layers, 80.0 x 35.3 mm, 38 parts (5 on the bottom side), 23 nets.

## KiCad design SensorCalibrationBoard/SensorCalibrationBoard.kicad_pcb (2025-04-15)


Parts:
C1, C2: 10uF; C_0805_2012Metric
FET1: PMV45EN2; SOT-23_Handsoldering
J1: Conn_01x05; PinHeader_1x05_P2.54mm_Vertical
LED1: TLCR5800; LED_D5.0mm_Horizontal_O1.27mm_Z3.0mm
PD2: BPW96B; LED_D5.0mm_Horizontal_O1.27mm_Z3.0mm
R1, R6: 220R; R_0805_2012Metric
R2: 100K; R_0805_2012Metric
R3: 10R; R_0805_2012Metric
R4: R56; R_0805_2012Metric
R5: R; R_Axial_DIN0207_L6.3mm_D2.5mm_P7.62mm_Horizontal
TR1: BC849; SOT-23_Handsoldering

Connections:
/ADC: J1.4, PD2.2 (E), R5.1
/LED_ON: J1.1, R1.1
GND: C1.2, C2.2, J1.3, R2.2, R4.2, R5.2, TR1.2 (E)
unnamed: FET1.3 (D), LED1.1 (K)
unnamed: FET1.1 (G), R1.2, R2.1, TR1.3 (C)
unnamed: FET1.2 (S), R4.1, TR1.1 (B)
unnamed: C1.1, LED1.2 (A), R3.2
unnamed: C2.1, PD2.1 (C), R6.1
Vbatt: J1.2, R3.1
Vcc: J1.5, R6.2

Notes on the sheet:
The RP2040 GPIO pins can support a max of 50mA TOTAL. RP2040 runs at 3.3v Each pin should not draw more than 16mA 3.3/0.016 = 206 Let's go higher and say 220R


Board: 2 copper layers, 18.0 x 35.0 mm, 13 parts (1 on the bottom side), 10 nets.

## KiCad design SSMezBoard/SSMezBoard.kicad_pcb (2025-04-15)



Board: 2 copper layers, 30.0 x 60.0 mm, 9 parts (2 on the bottom side), 27 nets.

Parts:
A1: Arduino_Nano_RP2040_Connect; Arduino_Nano
D1, D2: LED; LED_D5.0mm
J1: Conn_02x10_Odd_Even; PinHeader_2x10_P2.54mm_Horizontal
J2: Conn_01x02; PinHeader_1x02_P2.54mm_Vertical
J3: Conn_01x05; PinSocket_1x05_P2.54mm_Vertical
R1, R2: 1K; R_Axial_DIN0207_L6.3mm_D2.5mm_P7.62mm_Horizontal
SW1: TACT_SW; SW_PUSH_6mm

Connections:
D18_A6: A1.25 (A6), J1.18
GND: A1.4 (GND), A1.29 (GND), D1.1 (K), D2.1 (K), J1.20, J2.2, J3.5, SW1.1 (A)
GPIO_DIAG: A1.14 (D11/COPI), J1.8
GPIO_FRONT: A1.15 (D12/CIPO), J1.6
LEFT_DIAG_ADC: A1.22 (A3), J1.14
LEFT_ENC_A: A1.11 (D8), J1.3
LEFT_ENC_B: A1.12 (D9), J1.1
LEFT_FRONT_ADC: A1.21 (A2), J1.16
LEFT_Motor_Dir: A1.7 (D4), J1.11
LEFT_Motor_PWM: A1.6 (D3), J1.13
unnamed: A1.2 (D0/RX), R2.1
unnamed: A1.1 (D1/TX), J2.1, SW1.2 (B)
unnamed: A1.16 (D13/SCK), R1.2
unnamed: A1.24 (SCL/A5), J3.4
unnamed: A1.23 (SDA/A4), J3.3
unnamed: D1.2 (A), R2.2
unnamed: D2.2 (A), R1.1
RESET: A1.3 (~RESET), J1.17
RIGHT_DIAG_ADC: A1.19 (A0), J1.12
RIGHT_ENC_A: A1.9 (D6), J1.7
RIGHT_ENC_B: A1.10 (D7), J1.5
RIGHT_FRONT_ADC: A1.20 (A1), J1.10
RIGHT_Motor_Dir: A1.8 (D5), J1.9
RIGHT_Motor_PWM: A1.5 (D2), J1.15
SENSOR_LED: A1.13 (D10/CS), J1.4
Vbatt: A1.30 (VIN), J1.19, J3.2
Vcc: A1.17 (3V3), J1.2, J3.1

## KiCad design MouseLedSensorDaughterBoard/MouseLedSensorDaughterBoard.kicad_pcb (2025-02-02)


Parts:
J2: Conn_01x04; PinHeader_1x04_P2.54mm_Vertical
LED1: TLCR5800; LED_D5.0mm
PD2: QSB34; PLCC_2L_Handsoldering
PD3: BPW96B; LED_D5.0mm_Clear

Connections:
/LED+: J2.2, LED1.2 (A)
/LED-: J2.1, LED1.1 (K)
/Sen+: J2.3, PD2.1 (K), PD3.1 (C)
/Sen-: J2.4, PD2.2 (A), PD3.2 (E)


Board: 2 copper layers, 13.0 x 25.0 mm, 4 parts (0 on the bottom side), 4 nets.

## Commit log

2025-01-25 Boards init checkin
    [MouseLedSensorDaughterBoard.kicad_pcb, MouseLedSensorDaughterBoard.kicad_sch, MouseLedSensorMainBoard.kicad_pcb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]
2025-01-29 Updates based on feedback
    [BlankTemplate.kicad_pcb, BlankTemplate.kicad_sch, MouseSMDSensorBoard.kicad_pcb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]
2025-02-02 Sort of ready for JLCPCB
    [MouseLedSensorDaughterBoard.kicad_pcb, MouseLedSensorDaughterBoard.kicad_sch, MouseSMDSensorBoard.kicad_pcb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]
2025-04-15 Version 2 of boards sent to JLCPCB and a new calibration board
    [GeminiArduinoMez.kicad_pcb, GeminiArduinoMez.kicad_sch, MouseLedSensorMainBoard-EdgeCuts.dxf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]
2025-08-15 Checkin to baseline everything
    [DcBoost.kicad_pcb, DcBoost.kicad_sch, SSChassisAndSensorBoard.kicad_pcb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]
2025-08-15 KiCad Automation
2025-08-15 docs: update KiCad exports [skip ci]
    [BlankTemplate_bom.csv, DcBoost_bom.csv, GeminiArduinoMez_bom.csv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]
2025-08-19 Send boards to JLCPCB
    [SSEverythingMainBoard.kicad_pcb, SSEverythingMainBoard.kicad_sch]
2025-12-11 updates before complete rearrange
    [SSEverythingMainBoard-EdgeCuts.dxf, SSEverythingMainBoard-PasteBottom.dxf, SSEverythingMainBoard-PasteTop.dxf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]
2026-01-22 before updating to KiCad 9 and changing sensor design
    [SSEverythingMainBoard.kicad_sch, SSEverythingMainBoardv2.kicad_pcb, SSEverythingMainBoardv2.kicad_sch]
2026-01-29 first draft of new board all layout complete
    [SSEverythingMainBoardv2.kicad_pcb, SSEverythingMainBoardv2.kicad_sch]
2026-01-30 update workflow to use kicad 9
2026-01-31 First version of v4 board ready for production
    [SSEverythingMainBoardv2.kicad_pcb, SSEverythingMainBoardv2.kicad_sch]
2026-02-03 updated sensor locations, all resistors are back to be 0805, routing changes and moved the motor controller around plus other changes from Peter's suggestions
    [SSEverythingMainBoardv2.kicad_pcb, SSEverythingMainBoardv2.kicad_sch]
2026-02-03 routing changes
    [SSEverythingMainBoardv2.kicad_pcb, SSEverythingMainBoardv2.kicad_sch]
2026-02-04 trace tweaks
    [SSEverythingMainBoardv2.kicad_pcb]
2026-02-08 New board sent to JLCPCB for new Chassis
    [SSEverythingMainBoardv2.kicad_pcb, SSEverythingMainBoardv2.kicad_sch]
